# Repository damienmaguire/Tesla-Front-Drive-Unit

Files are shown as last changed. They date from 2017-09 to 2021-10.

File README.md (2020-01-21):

# Tesla-Front-Drive-Unit
Open Source Logic board to control the Tesla Model S Front Drive Unit
This board replaces the Tesla OEM control board in the high efficency front drive unit
and enables full control of the inverter and motor using simple analog / digital and CAN communication. Design files in DesignSpark 8 format.

Software may be downladed here:
https://github.com/jsphuebner/stm32-sine/releases

Fully built and tested boards and bare PCBs available here : http://www.evbmw.com/index.php/evbmw-webshop

Support forum : https://openinverter.org/forum/

23/09/17 : Released V1 schematic for the logic board. Untested. Also released pinout for the logic to igbt board interface header and Autocad dxf of the board outline with critical component locations.

02/10/17 : Released V1 design files. Untested. Unproven. Educational use only.

06/11/17 : V1 board bench tested and working well. No in car testing as yet.

29/12/17 : Uploaded V2 design files for small drive unit logic board. Compatible with both front and rear small Tesla drive units.

Just one change :

ULN2003 replaced by NCV8401ADT for driving precharge relay and main contactor following in car testing of the large drive unit.

Happy new year :)

14/08/18 : Following some excellent testing and investigation by a european customer, V3 design files are released. Small changes to component values in the current sensor opamp circuit as well as addition of two filter capacitors in the same. Now running well in vehicle. Also uploaded working parameter file.

18/10/18 : Two customers reported failures of their inverter when using the V2 board. One customer reported they had fixed the issue but then refused to share the details. I have worked with the second customer in Romania on the problems. Here are some details :

Root cause of the drive unit inverter failures discovered and fixed.
NOT caused by overcurrent through the igbts but rather the combination of using 8.8kHz switching frequency through a very low inductance stator and the sudden release of the main contactor on an overcurrent detection. The small drive unit inverter works perfectly at 17.6khz switching frequency and setting tripmode to prechon ensures the pre charge resistor can provide a path back to the battery during release of the main contactor. This was tested to the Nth degree on my recent trip to Romania

Working on a fix for a hardware bug that is limiting power. The tesla current sensors span +/- 1250A over a range of 0-5v with 2.5v representing 0A. Seems Tesla use the EXACT SAME hardware overcurrent detection circuit on their logic board as designed by Johannes. They set trip points at .1V and 4.9V giving a total span of 1200A. (1A=2mV). The component choice in the opamp circuit on the open source board causes a hardware overcurrent event at +850A regardless of settings above this value thus limiting power. It was this trip coupled with the above issues relating to main contactor control and switching frequency that lead to inverter deaths.

Identified the hall effect current sensor used in the small drive units as the MLX91209. So at least now if I wreck one they only cost 3 Euros to replace. A V4 design will be released shortly along with details on how to modify the V2 and V3 boards to avoid this problem. 

28/10/18 : V4 Design files released. Major changes : 

Updated current sensor opamp component values to allow the full +/-1200A swing.

Deleted the encoder polarity jumper as no longer needed.

Added option to fit ESP WiFi module on board (untested)

Added jumper to disable RS232 Transciever (required if using on board wifi)

Latest sourcecode and binaries will available from https://github.com/jsphuebner/stm32-sine

V2 and V3 boards can still be used by changing the following component values : R44,R49 = 62k, R48 = 3k16.

On the web interface set the following two parameters :

PWMFRQ=17.6kHz

Tripmode = Prechon

Working and tested full parameter files will be released shortly.

29/10/18 : V2 Design files and BOM updated for modifications and also incorrect values for temp sensor load resistors in BOM.

Test run with modification : https://www.youtube.com/watch?v=mhGwcPWCbsA

21/01/20 : V6 design files now released. Both fully built and partial built boards available from the EVBMW webshop : https://www.evbmw.com/index.php/evbmw-webshop
Don't want to buy from me and support ongoing development? That's ok as this release also includes the BOM, CPL and Gerber files needed to build your own at JLCPCB : https://jlcpcb.com

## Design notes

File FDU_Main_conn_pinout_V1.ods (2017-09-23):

Tesla Small Drive Unit Main Connector Pinout
Pin Number | Function | Signal Description
1 | CAN LOW | Can bus low signal
2 | CAN HIGH | Can bus high signal
3 | MAIN CONTACTOR CONTROL | Open collector control for main HVDC contactor
4 | ACCELERATOR +5V | +5v dc supply for accelerator / throttle
5 | FORWARD DIRECTION SIGNAL | When pulled to +12v motor will run forward
6 | ACCELERATOR GROUND | Ground connection for accelerator / throttle
7 | BRAKE TRANSDUCER GROUND | Ground connection for brake pedal position sensor
8 | ACCELERATOR SIGNAL | Input for accelerator / throttle signal. 0-3.3v span.
9 | START SIGNAL | Starts the inverter when connected briefly to +12v. Typically connected to “Start” position on car ignition switch
10 | BRAKE TRANSDUCER SIGNAL | Signal from brake pedal position sensor. 0-3.3v span. Controls regen relative to brake pedal position
11 | PRECHARGE RELAY CONTROL | Open collector control for main HVDC precharge relay
12 | REVERSE DIRECTION SIGNAL | When pulled to +12v motor will run in reverse
13 | +12V SUPPLY IGN ON | Main +12v dc supply to inverter
14 | RS232 Rx | Serial receive line for RS232 communication
15 | BRAKE ON DIGITAL SIGNAL | +12v signal to inverter that brake pedal is pressed
16 | RS232 Tx | Serial transmit line for RS232 communication
17 | CRUISE CONTROL SIGNAL | Toggles cruise control on and off with +12v momentary signal
18 | BRAKE TRANSDUCER +5V | +5v dc supply for brake pedal position transducer
19 | GROUND | Main system ground to chassis of vehicle
20 | TACHOMETER DRIVE SIGNAL | Open collector variable frequency drive for standard tachometer

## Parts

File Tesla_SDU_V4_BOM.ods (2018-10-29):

Tesla Small Drive Unit Logic Board V4
Ref Name | Qty | Component | Value | Manufacturer | MPN | Farnell Part Number | Mouser Part number | Description
CONN7,9,8,SWPROG | 4 | 2SIL |  | AMPHENOL FCI | 77311-401-36LF | 1097954 |  | Board-To-Board Connector, 2.54 mm, 36 Contacts, Header, BergStik 77311 Series, Through Hole, 1 Rows
CONN10 | 1 | 75867-101LF |  | FCI | 75867-101LF | 6737635 |  | 10w R/A T/H boxed header Quickie Amphenol FCI Quickie Series, 2.54mm Pitch 10 Way 2 Row Shrouded Right Angle PCB Header, Through Hole
IC11 | 1 | 74HCT4052D |  | NXP | 74HCT4052D | 4836730 |  | 74HCT4052D, Multiplexer/Demultiplexer Dual 4:1, 5 V, 16-Pin, SOIC, 2
CONN2 | 1 | 75757-5101 |  | Molex | 75757-5101 |  | 538-75757-5101 | Headers & Wire Housings MX150 2X10 VERT HEAD HEADER ASSY 2.5 TIN
L1 | 1 | 7447709470 |  | Wurth Elektronik | 7447709470 | 1635946 |  | SMD-Shielded Power Inductors WE-PD
IC10 | 1 | ADM3101EARQZ |  | Analog Devices | ADM3101EARQZ | 7097966 |  | ADM3101EARQZ, Line Transceiver, EIA-232-E, RS-232, V.28, 3.3 V, 16-Pin QSOP
C41,23,24,106,44,42,43,45,36,4,8,10,11,16,65 | 15 | C-USC0805 | 0.1uF | MURATA | GRM219R71C104KA01D | 2611934 |  | Murata 0805 GRM 100nF Ceramic Multilayer Capacitor, 16 V dc X7R Dielectric ±10% SMD
C18,19,20,33,34 | 5 | C-USC0805 | 1nF | MULTICOMP | MCSH21B102K160CT | 1856432 |  | SMD Multilayer Ceramic Capacitor, 0805 [2012 Metric], 1000 pF, 16 V, ± 10%, X7R, MCSH Series
C21,22,25,26,28,29,30,31,32,57,58,59,60,61,62,6,7,14,15,37 | 20 | C-USC0805 | 1uF | KEMET | C0805C105K4RACTU | 9227792 |  | Kemet 0805 1μF Ceramic Multilayer Capacitor, 16V dc X7R Dielectric ±10% SMD
C46,47,48,49,50 | 5 | C-USC0805 | 10nF | Wurth Elektronik | 885012207039 | 2534055 |  | SMD Multilayer Ceramic Capacitor, 0805 [2012 Metric], 0.01 µF, 16 V, ± 10%, X7R,
C1,2 | 2 | C-USC0805 | 27pF | MULTICOMP | MC0805N270J500CT | 1759196 |  | SMD Multilayer Ceramic Capacitor, 0805 [2012 Metric], 27 pF, 50 V, ± 5%, C0G / NP0, MC Series
C105 | 1 | C-USC0805 | 47nF | YAGEO (PHYCOMP) | CC0805KRX7R9BB473 | 718683 |  | SMD Multilayer Ceramic Capacitor, 0805 [2012 Metric], 0.047 µF, 50 V, ± 10%, X7R, CC Series
C3 | 1 | Cap_el | 100uF | MULTICOMP | MCMR6V3107M6.3X7 | 9452567 |  | Electrolytic Capacitor, 100 µF, 6.3 V, MCMHR Series, ± 20%, Radial Leaded, 6.3 mm
IC5 | 1 | CD74HC30M |  | Texas Instruments | CD74HC30M | 526824 |  | CD74HC30M, Logic Gate 8 Input NAND, HC, 5.2mA 2 to 6V 14-Pin SOIC
X2 | 1 | CRYSTALTC26HM | 32.768kHz | RALTRON | R26-32.768- 12.5 | 1652573 |  | Crystal, 32.768 kHz, Cylinder Radial, 6.2mm x 2mm Dia, 12.5 pF, 20 ppm, R26 Series
C12,13 | 2 | C_0805 | 10pF | Wurth Elektronik | 885012007010 | 2533859 |  | SMD Multilayer Ceramic Capacitor, 0805 [2012 Metric], 10 pF, 16 V, ± 5%, C0G / NP0
C5,9,17 | 3 | C_0805 | 10uF | MURATA | GRM21BR61E106KA73L | 1735530 |  | SMD Multilayer Ceramic Capacitor, 0805 [2012 Metric], 10 µF, 25 V, ± 10%, X5R, GRM Series
C38 | 1 | EEEFK1A221XP | 220uF | Panasonic | EEEFK1A221XP | 7083342 |  | Ecap 220uF 10V D8 Case FK SMD Panasonic 220F 10 V dc Aluminium Electrolytic Capacitor, FK SMD Series 2000h 6.3 Dia. x 7.7mm
C35 | 1 | EEVEB2C680SM | 680uF | Panasonic | EEVEB2C680SM | 2326340 | 667-EEV-EB2C680SM | PANASONIC ELECTRONIC COMPONENTS - EEVEB2C680SM - CAP, ALU ELEC, 68UF, 160V, SMD
C27,39 | 2 | C-USC0805 | 50pF | YAGEO (PHYCOMP) | CC0805JRNPO9BN470 | 1362560 |  | SMD Multilayer Ceramic Capacitor, 0805 [2012 Metric], 47 pF, 50 V, ± 5%, C0G / NP0, CC Series
CONN1 | 1 | FDU_IGBT_CONN |  | 3M | 929975-01-36 | 828-2058 |  | 3M 929 Series 929975 Series Number 2.54mm Pitch 72 Way 2 Row Straight PCB Header
LD1 | 1 | LD1117SOT223 | LD1117-3.3 | STMICROELECTRONICS | LD1117S33CTR | 1467779 |  | Fixed LDO Voltage Regulator, 4.75V to 15V, 1.1V Dropout, 3.3Vout, 950mAout, SOT-223-4
LED1,2 | 2 | LED0805 |  | MULTICOMP | MCL-S270GC | 1581242 |  | LED, Green, SMD, 1.25mm x 1.4mm, 20 mA, 2.1 V, 570 nm
X1 | 1 | LFXTAL011301 | 8.00MHz | IQD | LFXTAL011301 | 4789656 |  | Crystal SMD 8.000MHz HC49S-SMD Crystal 8MHz, 30ppm, 2-Pin HC-49-4H-SMX
IC8 | 1 | LM2596S-5.0_NOPB |  | Texas Instruments | LM2596S-5.0/NOPB | 5333692 |  | SIMPLE SWITCHER 4.5V to 40V, 3A Low Component Count Step-Down Regulator
IC4 | 1 | LM2901DT |  | STMicroelectronics | LM2901DT | 7140745 |  | LM2901DT, Quad Comparator Open Collector 1.3s 12 V, 15 V, 18 V, 24 V, 28 V, 3 V, 5 V, 9 V 14-Pin SO
L2 | 1 | L_PM0603 | 10uH | TDK | MLZ1608M100WT | 2215635 |  | Surface Mount High Frequency Inductor, MLZ Series, 10 µH, 250 mA, 0603 [1608 Metric], Multilayer
D1,D2 | 2 | MBRS540T3G |  | ON Semiconductor | MBRS540T3G | 1250012 |  | Diode Schottky 40V 5A SMC ON Semiconductor MBRS540T3G Schottky Diode, 5A, 40V, 2-Pin SMC
IC12 | 1 | MC74HCT573ADWR2G |  | ON Semiconductor | MC74HCT573ADWR2G | 2814898 | 863-MC74HCT573ADWR2G | TRANSPARENT LATCH, OCTAL, SOIC-20
IC7 | 1 | MCP602-I_SN |  | Microchip | MCP602-I/SN | 3792588 |  | Operational Amplifier, Dual, 2 Amplifier, 2.8 MHz, 2.3 V/µs, 2.7V to 5.5V
Q1 | 1 | MMBT3904 |  | Fairchild Semiconductor | MMBT3904 | 7390303 |  | Transistor GP BJT NPN 40V 0.2A SOT23 Fairchild MMBT3904 NPN Bipolar Transistor, 0.2 A, 40 V, 3-Pin SOT-23
R8,6,38,39,40,41,43,35 | 8 | R-US_R0805 | 1k | MULTICOMP | MC01W080551K | 9333711 |  | SMD Chip Resistor, Thick Film, 1 kohm, 150 V, 0805 [2012 Metric], 100 mW, ± 5%, MC Series
R24,26,28,32,33 | 5 | R-US_R0805 | 1K5 | Panasonic | ERJ6RBD1501V | 2380317 |  | SMD Chip Resistor, Thick Film, 1.5 kohm, 150 V, 0805 [2012 Metric], 100 mW, ± 0.5%, ERJ6E Series
R3,7,17 | 3 | R-US_R0805 | 3K3 | Panasonic | ERJ6RBD3301V | 2380370 |  | SMD Chip Resistor, Thick Film, 3.3 kohm, 150 V, 0805 [2012 Metric], 100 mW, ± 0.5%, ERJ6E Series
R48 | 1 | R-US_R0805 | 3K16 | Panasonic | ERJ6ENF3161V | 2303602 |  | SMD Chip Resistor, 3.16 kohm, ERJ6E Series, 150 V, Thick Film, 0805 [2012 Metric], 125 mW
R47,23,25,27,31,34,11 | 7 | R-US_R0805 | 4K7 | Panasonic | ERJ6RBD4701V | 2380397 |  | SMD Chip Resistor, Thick Film, 4.7 kohm, 150 V, 0805 [2012 Metric], 100 mW, ± 0.5%, ERJ6E Series
R2,4,9,10,12,14,15,46,51,1,18,19,20,21,29,30,36,37,13,22 | 20 | R-US_R0805 | 10k | BOURNS | CRT0805-FZ-1002ELF | 2008317 |  | SMD Chip Resistor, Thin Film, 10 kohm, 100 V, 0805 [2012 Metric], 100 mW, ± 1%, CRT Series
R65 | 1 | R-US_R0805 | 470K | VISHAY | CRCW0805470KFKEA | 1653006 |  | SMD Chip Resistor, 470 kohm, CRCW Series, 150 V, Thick Film, 0805
R16 | 1 | R-US_R0805 | 47K | Panasonic | ERJ6RBD4702V | 2380398 |  | SMD Chip Resistor, Thick Film, 47 kohm, 150 V, 0805 [2012 Metric], 100 mW, ± 0.5%, ERJ6E Series
R55,62,63,64,66 | 5 | R-US_R0805 | 150K | YAGEO (PHYCOMP) | RC0805FR-07150KL | 9237895 |  | SMD Chip Resistor, 150 kohm, RC Series, 150 V, Thick Film, 0805
R69,70 | 2 | R-US_R0805 | 60R4 | TE CONNECTIVITY | RN73C2A60R4BTDF | 2688288RL |  | SMD Chip Resistor, Precision, 60.4 ohm, 100 V, 0805 [2012 Metric], 100 mW, ± 0.1%
R45,50 | 2 | R-US_R0805 | 100K | MULTICOMP | MC01W08055100K | 9333738 |  | SMD Chip Resistor, 100 kohm, 150 V, 0805 [2012 Metric], 100 mW, ± 5%, MC Series
R44,49 | 2 | R-US_R0805 | 62K | VISHAY | CRCW080562K0FKEA | 2139013 |  | SMD Chip Resistor, 62 kohm, CRCW Series, 150 V, Thick Film, 0805 [2012 Metric], 125 mW
R42 | 1 | R-US_R0805 | 100R | MULTICOMP | MC01W08055100R | 9333703 |  | SMD Chip Resistor, Thick Film, 100 ohm, 100 V, 0805 [2012 Metric], 100 mW, ± 5%, MC Series
R5 | 1 | R-US_R0805 | 470R | Panasonic | ERJ6RBD4700V | 2380396 |  | SMD Chip Resistor, Thick Film, 470 ohm, 150 V, 0805 [2012 Metric], 100 mW, ± 0.5%, ERJ6E Series
R56,57,58,59,60 | 5 | R-US_R0805 | 560R | VISHAY | CRCW0805560RFKEA | 1469945 |  | SMD Chip Resistor, Thick Film, 560 ohm, 150 V, 0805 [2012 Metric], 125 mW, ± 1%
CONN3,4 | 2 | S02BA-AIT2-1AK |  | JST Automotive | S02BA-AIT2-1AK |  | 306-S02BA-AIT2-1AK | Automotive Connectors 2P BLK Side Entry Brs tin plated pin
CONN5 | 1 | S06B-AIT2-1AK |  | JST Automotive | S06B-AIT2-1AK |  | 306-S06B-AIT2-1AK | Automotive Connectors 6CIR BLK SNGL ROW SIDE ENTRY
IC9 | 1 | SN65HVD234 | SN65HVD234 | TEXAS INSTRUMENTS | SN65HVD234D | 1212363 |  | CAN Bus, Transceiver, CAN, 1, 1, 3 V, 3.6 V, SOIC
IC1 | 1 | STM32F103 | STM32F103RBT6 | STMICROELECTRONICS | STM32F103RBT6 | 1447640 |  | ARM Microcontroller, Motor Control, ARM Cortex-M3, 32bit, 72 MHz, 128 KB, 20 KB, 64 Pins
CONN6 | 1 | T821120A1S100CEU |  | AMPHENOL | T821120A1S100CEU | 8323499 |  | HEADER, VERTICAL, 2.54MM, 20WAY
IC13,IC14 | 2 | NCV8401ADTRKG |  | ON Semiconductor | NCV8401ADTRKG | 8079877 |  | Power Load Distribution Switch IC, Low Side, 1 Output, ± 14 V in, 16 A, 0.034 ohm

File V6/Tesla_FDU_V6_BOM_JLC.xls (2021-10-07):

Comment | Designator | Footprint | LCSC Part #
74HCT4052D | IC6 | SOIC-16_3.9x9.9x1.27P | C87281
BTS133TC | IC9,IC11 | TO-263-2 | C152447
0.1uF | C4,C13,C20,C39,C28,C30,C1,C2,C6,C13,C35,C52 | 0805_C | C49678
1nF | C18,C22,C29,C8,C5 | 0805_C | C46653
1uF | C27,C25,C32,C19,C17,C21,C40,C42,C45,C43,C46,C41,C44,C14,C11,C38,C36,C31,C37,C51 | 0805_C | C28323
10nF | C16,C9,C10,C12,C15 | 0805_C | C1710
22PF | C23,C24 | 0805_C | C1804
50pF | C3,C7 | 0805_C | C1716
CD74HC30M | IC5 | SOIC-14_3.9x8.7x1.27P | C5631
10pF | C26,C33 | C_0805 | C1785
10uF | C34,C48 | 0805_C | C15850
LD1117-3.3 | LD1 | SOT-223 | C347229
RED LEDS | LED1,LED2 | CHIPLED_0805 | C84256
5V REG | IC12 | TO-263-5 | C10002
LM2901DT | IC4 | SOIC-14_3.9x8.7x1.27P | C142961
10uH | L1 | 0603 | C1035
MC74HCT573ADWR2G | IC7 | SOIC-20_7.5x12.8x1.27P | C6000
MCP602-I_SN | IC3 | SOIC-8_3.9x4.9x1.27P | C29605
MMBT3904 | Q1 | SOT-23-3 | C20526
1KΩ | R23,R28,R39,R40,R34,R32,R38 | 0805_R | C17513
1.5KΩ | R43,R47,R53,R49,R55 | 0805_R | C4310
3.3KΩ | R31,R12,R10 | 0805_R | C26010
3.16KΩ | R7 | 0805_R | C52603
4.7KΩ | R36,R42,R46,R52,R48,R54,R8 | 0805_R | C17673
10KΩ | R5,R6,R22,R25,R44,R50,R45,R51,R20,R16,R15,R3,R1,R61,R60,R59,R58,R57,R56,R35 | 0805_R | C17414
47kΩ | R62 | 0805_R | C17713
62KΩ | R9,R11 | 0805_R | C17783
100KΩ | R2,R4 | 0805_R | C17407
100Ω | R27 | 0805_R | C17408
120Ω | R37 | 0805_R | C17437
150kΩ | R30,R33,R24,R21,R26 | 0805_R | C17470
470Ω | R41 | 0805_R | C17710
470kΩ | R29 | 0805_R | C17709
560Ω | R18,R13,R14,R17,R19 | 0805_R | C28636
SN65HVD234 | IC10 | SOIC-8_3.9x4.9x1.27P | C99818
SS54 | D1,D2 | SMA,DO-214AC | C22452
STM32F103RBT6 | IC8 | LQFP-64_10.0x10.0x0.5P | C8735
470UH | L2 | SMD-PIND-12.5x12.5x8_2.9x5.4 | C169382
100UF 6.3V | C50,C49,C47 | CASE-B_3528 | C16133
470uF 25V | C53 | SMD-ECAP-10x10 | C249931
8MHz | X1 | SMD-5032_2P | C115962

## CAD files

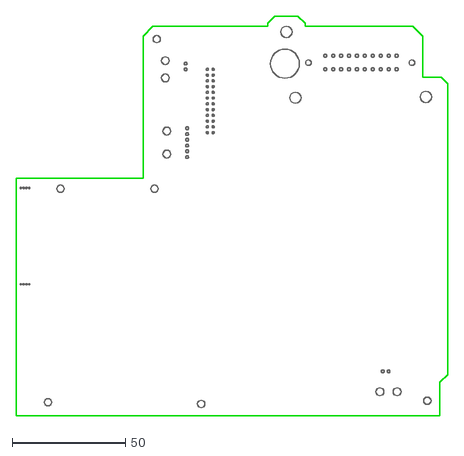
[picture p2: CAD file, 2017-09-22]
Tesla_FDU_V1.dxf
190.5 x 176.5

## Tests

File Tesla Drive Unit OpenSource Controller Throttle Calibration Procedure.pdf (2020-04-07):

## Tesla Drive Unit OpenSource Controller Throttle Calibration Procedure

Now to calibrate the throttle pedal so the inverter knows the range to expect.
Power on the inverter 12v supply (no High voltage needed at this point) and connect with WiFi.
The default WiFi settings are :
SSID : inverter
Passphrase : inverter123
Open a Web browser and enter 192.168.1.4 in the address bar and press enter.
Ensure the throttle pedal is properly connected to the inverter using pins 12 (+5V), 13 (signal), and 15 (ground).

With the throttle pedal at zero (ie no pressure on the pedal) scroll down to the “Pot”
Spot value on the webpage (make sure to refresh the webpage by pressing F5 or the “refresh” button). Make a note of this value.
Now press the throttle fully and repeat this process, again observing the ‘pot’ spot value.
Note this value. You now have the two values representing no throttle and full throttle.

Under the ‘Throttle’ category on the web interface, find the “PotMin” parameter and enter the value you recorded for zero throttle position (it is a good idea to make this value a few points less to allow for noise. So if you recorded 850 then put in 830 for “PotMin”). Don’t forget to press enter. Now find “PotMax” and do the same as above but use the full throttle value. Press enter.

Scroll to the top and click the “Save parameters to flash” button.
Turn the 12v power to the inverter off and then on after a few seconds and check the throttle value is now correct.

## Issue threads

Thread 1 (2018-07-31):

C35 Footprint is smaller than the component. Components around it touch with it.

annerajb, 2018-07-31:
Hey,

Got around to build your board (currently trying to program/flash)
Found a issue The footprint area for the C35 part is smaller than the actual part (or the part number is incorrect) There are two versions of that Capacitor one is 16.5 MM tall the other one is 18.9MM (and smaller diameter)

The bom calls for the 16.5MM tall one which makes it wider and touches / dosn't fir the pcb layout under it.

I would fix it but not sure if it's a part number mistake, foot print is incorrect or is there any other intended reason for this.

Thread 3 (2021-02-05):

C47 not connected to ground. Incorrect net.

Bedz01, 2021-02-05:
I was testing a PCB that I just put together and noticed the capacitor C47 is not connected to ground.
I looked the the schematic and it turns out that the "GND" symbol is not assigned to the GND net, but rather to N0165.
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

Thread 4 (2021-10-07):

BOM and CPL files no longer valid for JLCPCB SMT quoting

DocOnGitHub, 2021-10-07:
Recently JLCPCB has changed the headers in their BOM and CPL files to use the term "Footprint" instead of "Package". The current files produce this error on upload:

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

Closed 2021-10-07.

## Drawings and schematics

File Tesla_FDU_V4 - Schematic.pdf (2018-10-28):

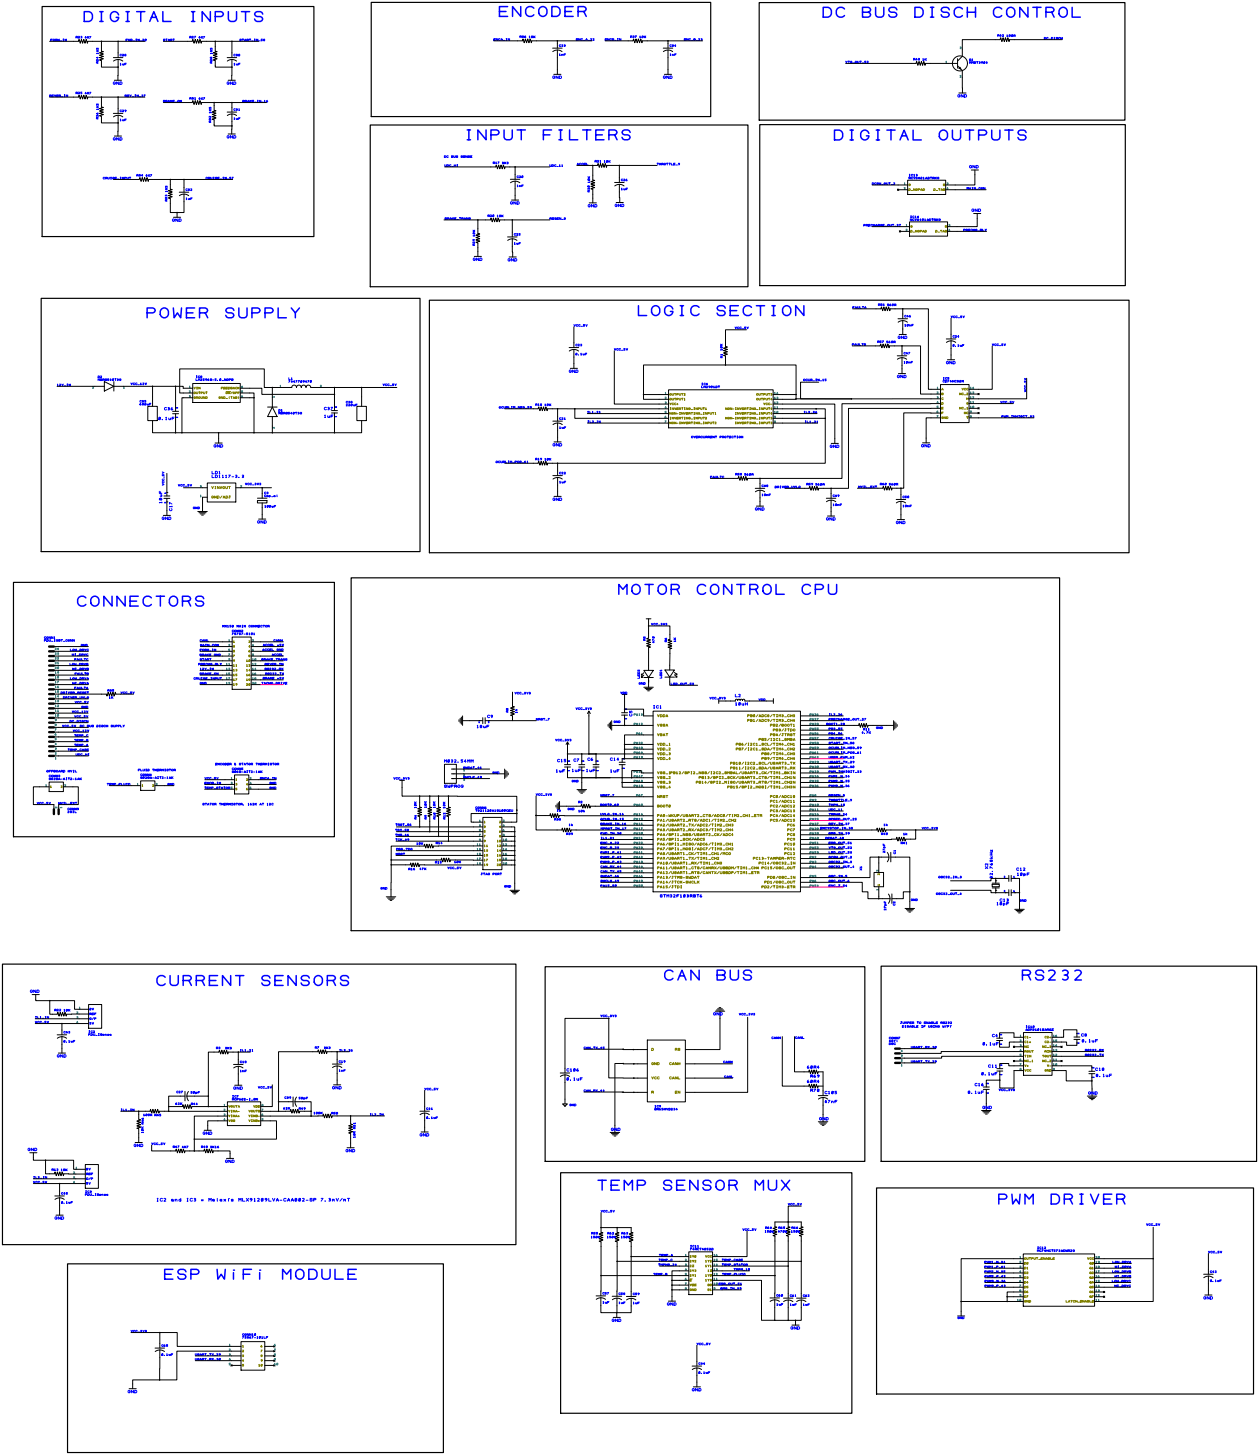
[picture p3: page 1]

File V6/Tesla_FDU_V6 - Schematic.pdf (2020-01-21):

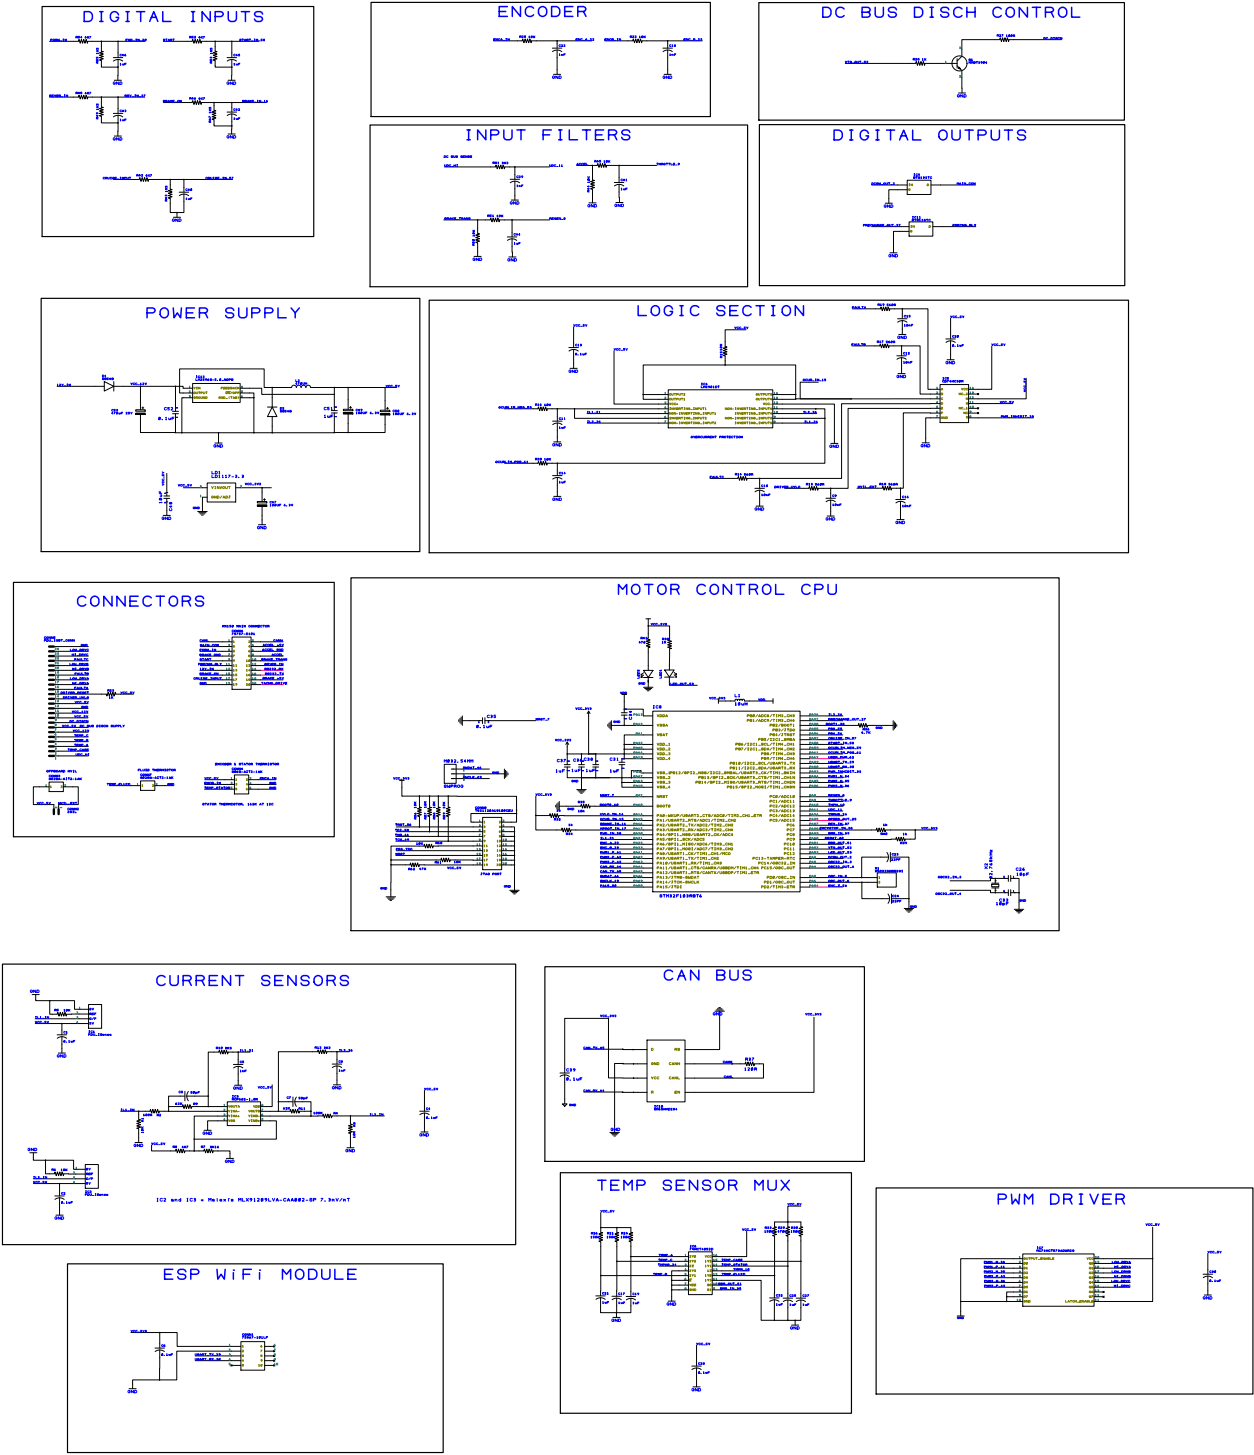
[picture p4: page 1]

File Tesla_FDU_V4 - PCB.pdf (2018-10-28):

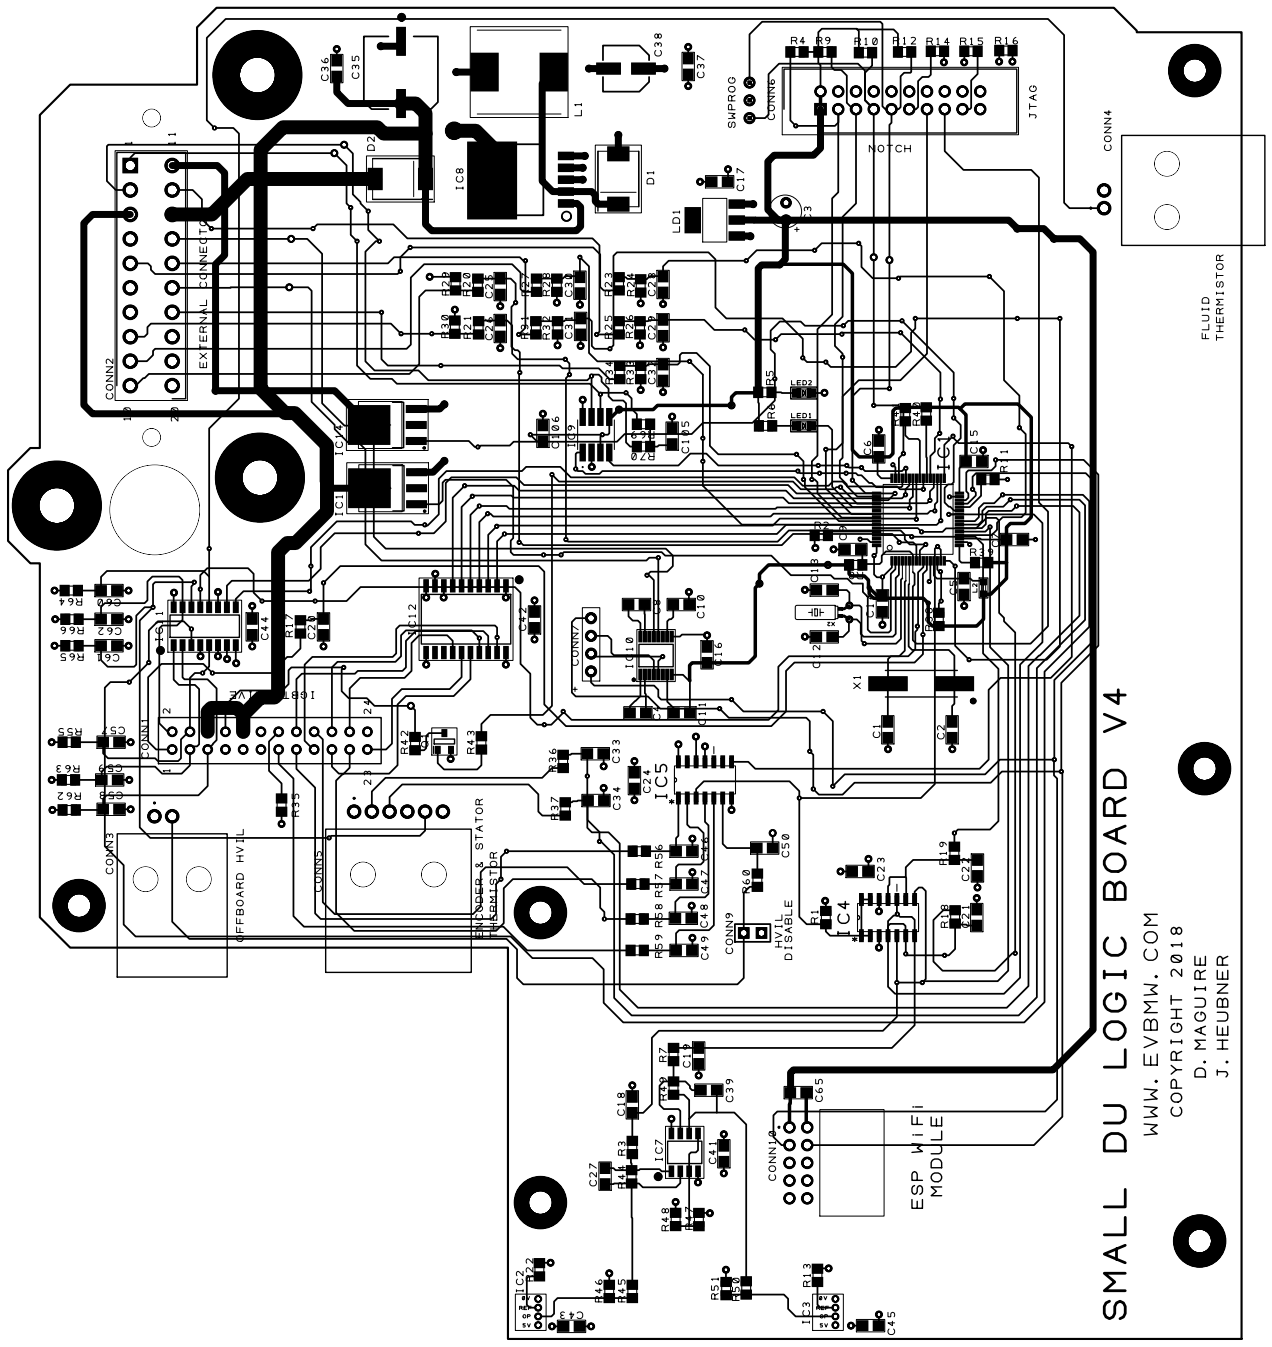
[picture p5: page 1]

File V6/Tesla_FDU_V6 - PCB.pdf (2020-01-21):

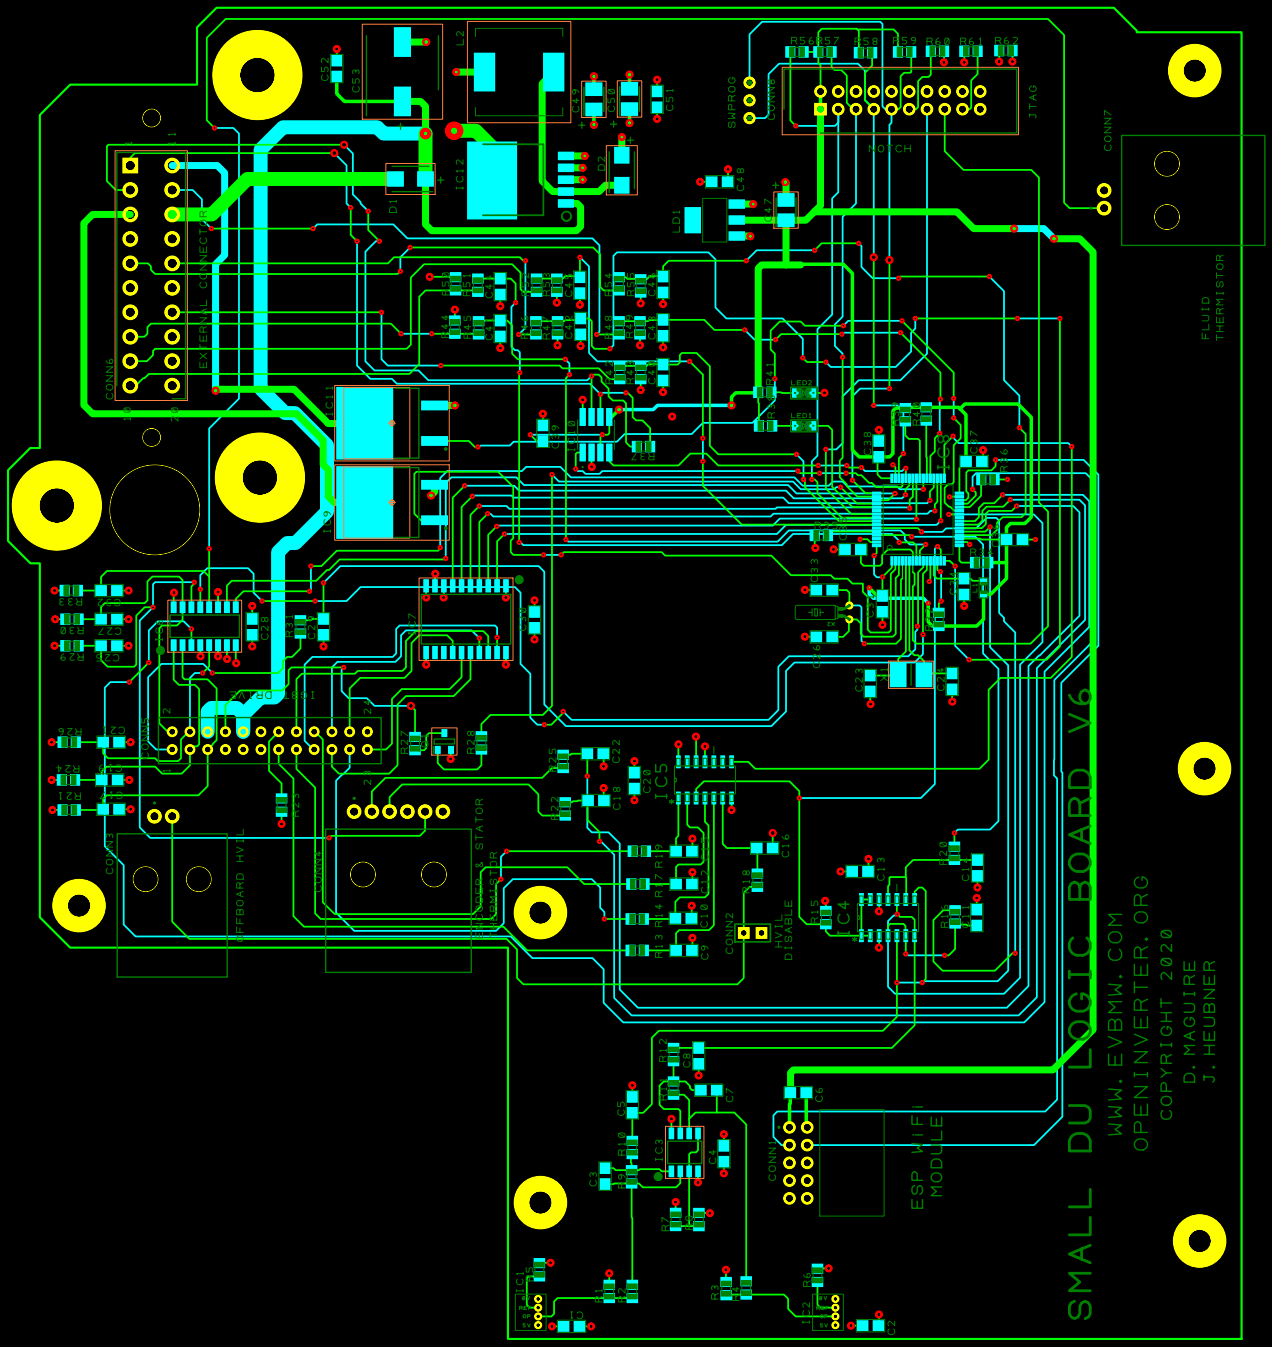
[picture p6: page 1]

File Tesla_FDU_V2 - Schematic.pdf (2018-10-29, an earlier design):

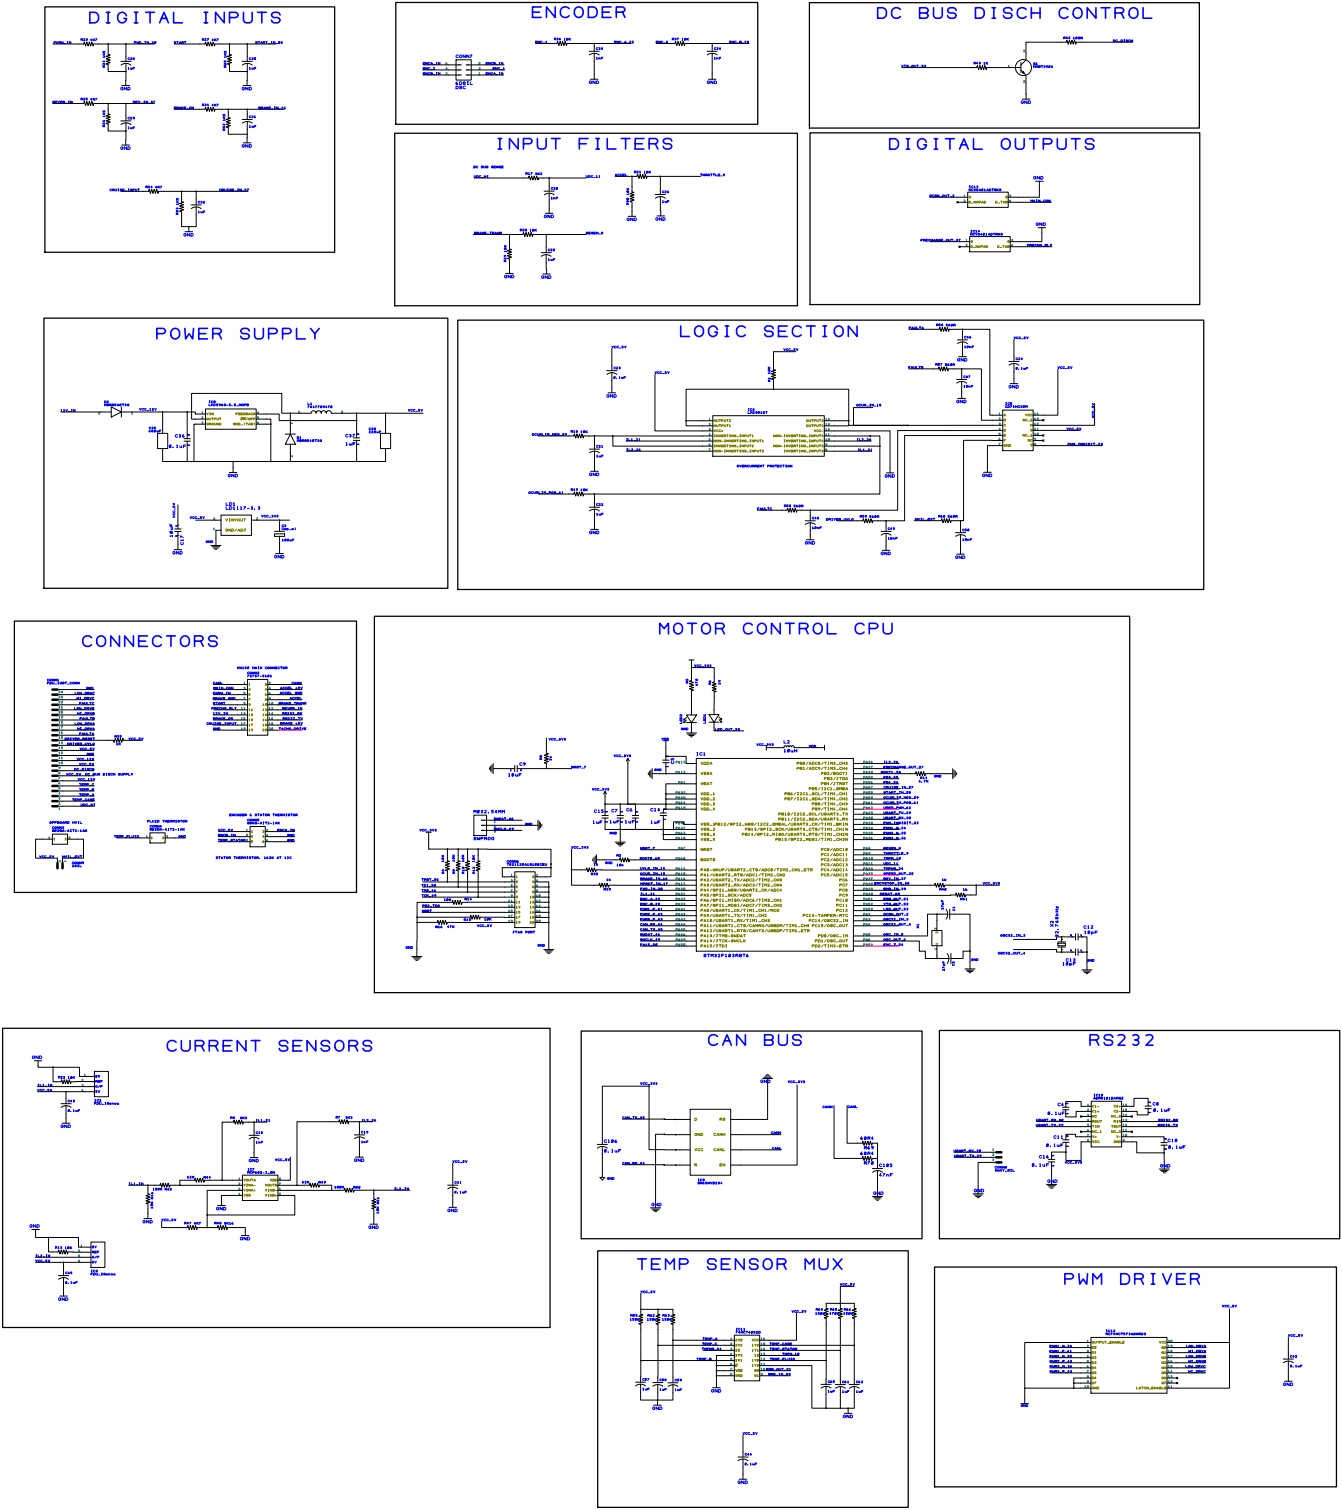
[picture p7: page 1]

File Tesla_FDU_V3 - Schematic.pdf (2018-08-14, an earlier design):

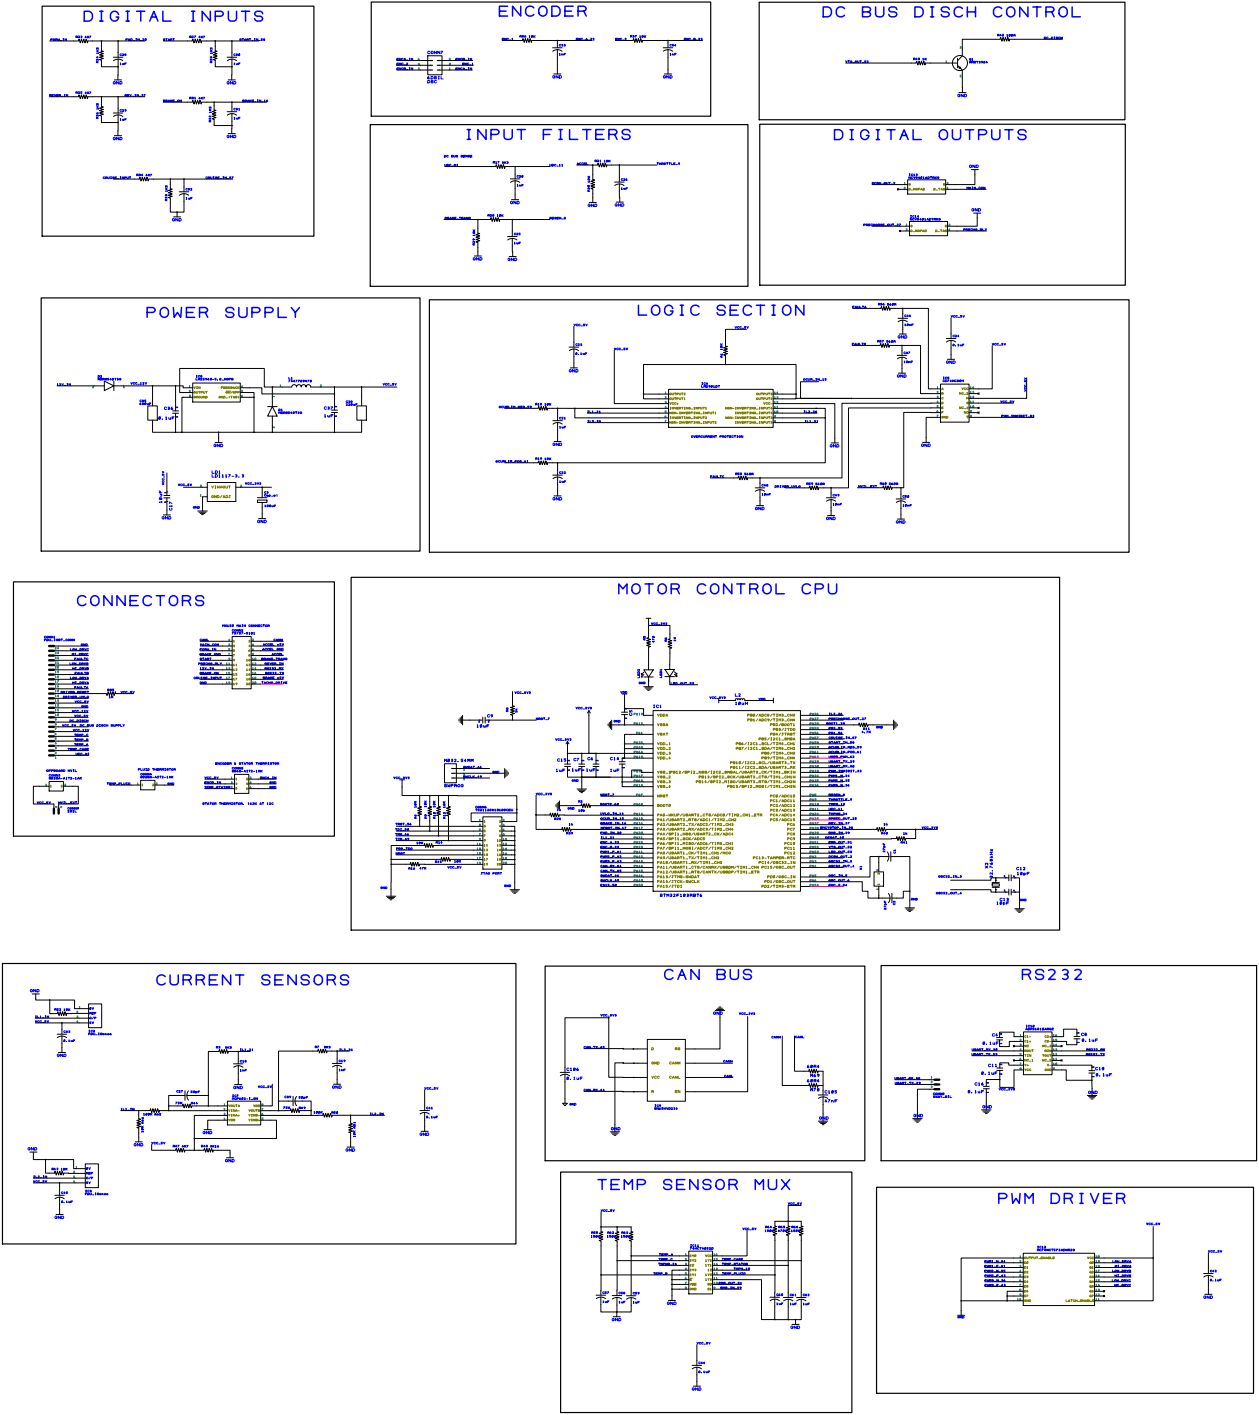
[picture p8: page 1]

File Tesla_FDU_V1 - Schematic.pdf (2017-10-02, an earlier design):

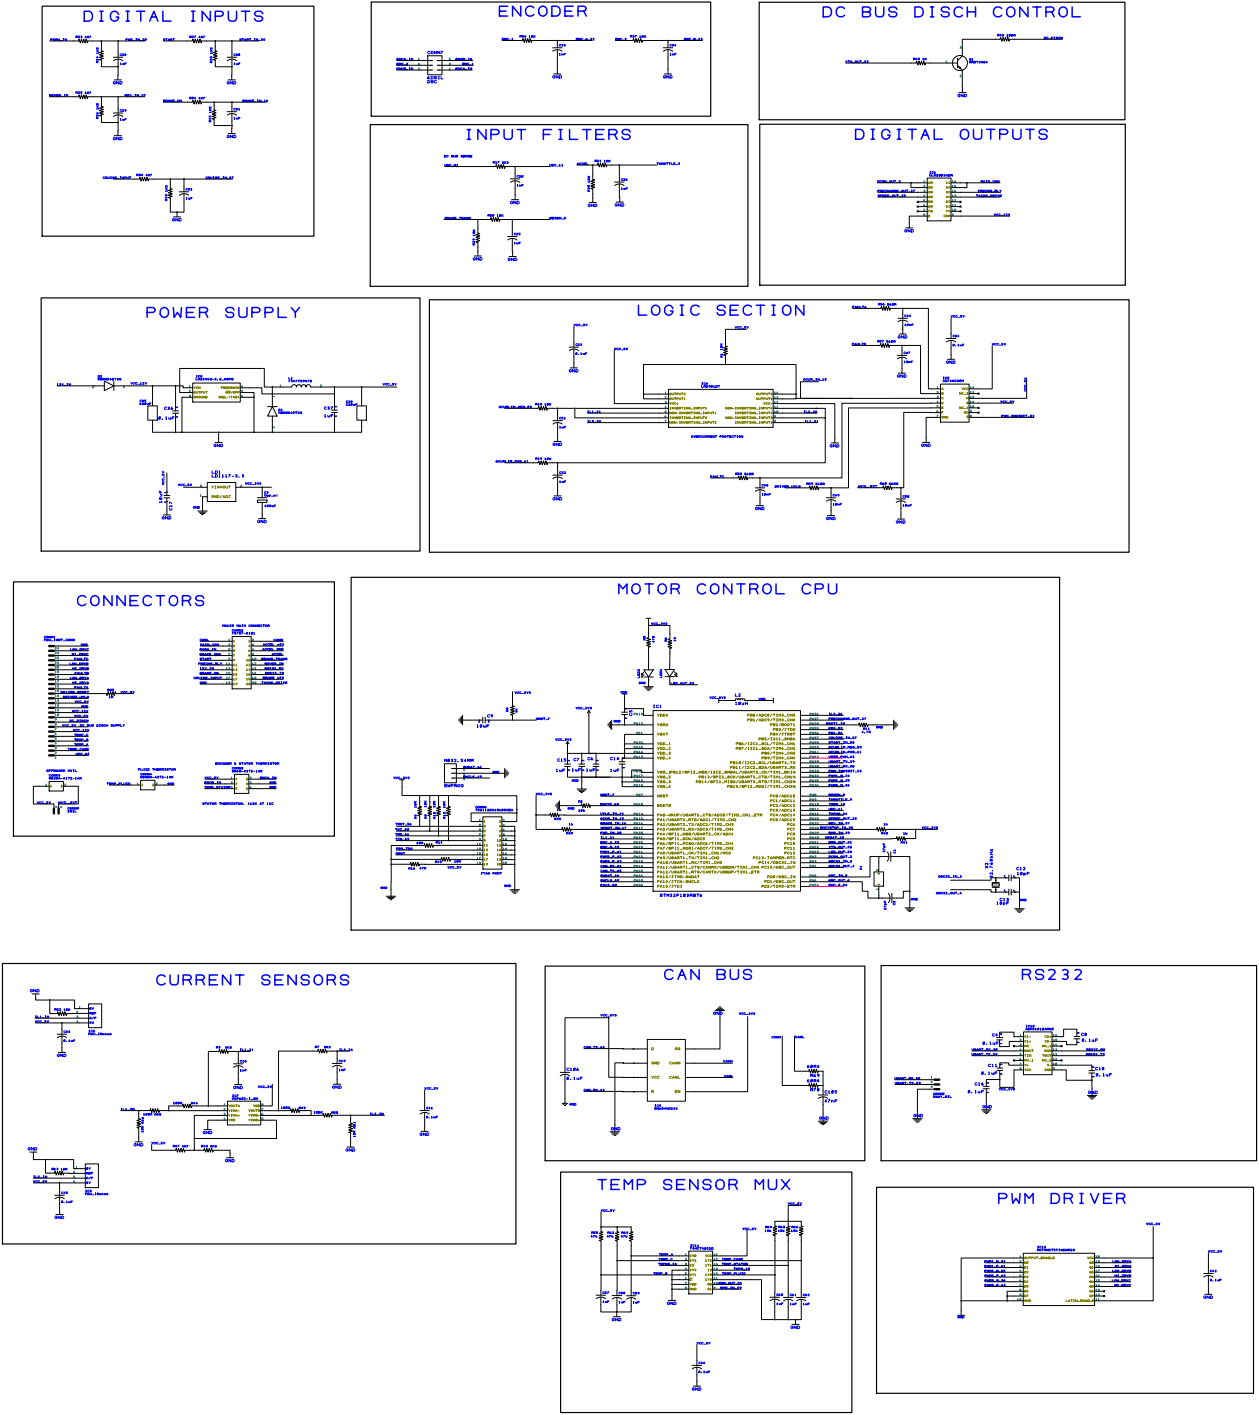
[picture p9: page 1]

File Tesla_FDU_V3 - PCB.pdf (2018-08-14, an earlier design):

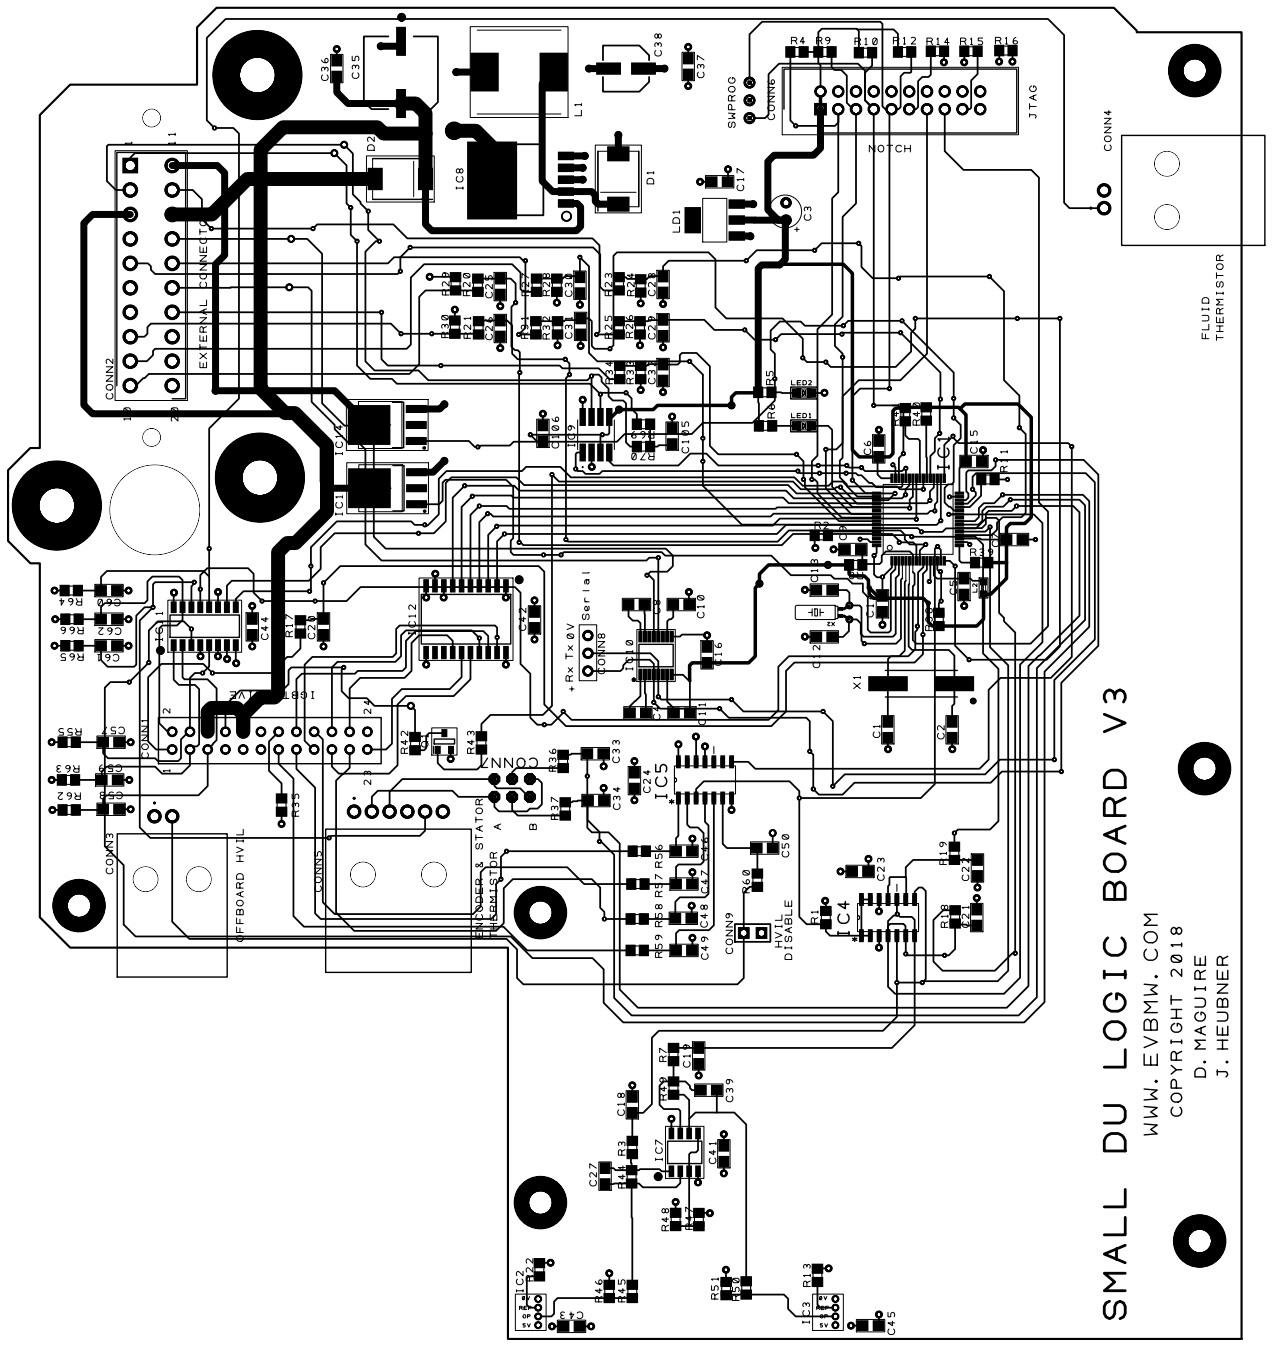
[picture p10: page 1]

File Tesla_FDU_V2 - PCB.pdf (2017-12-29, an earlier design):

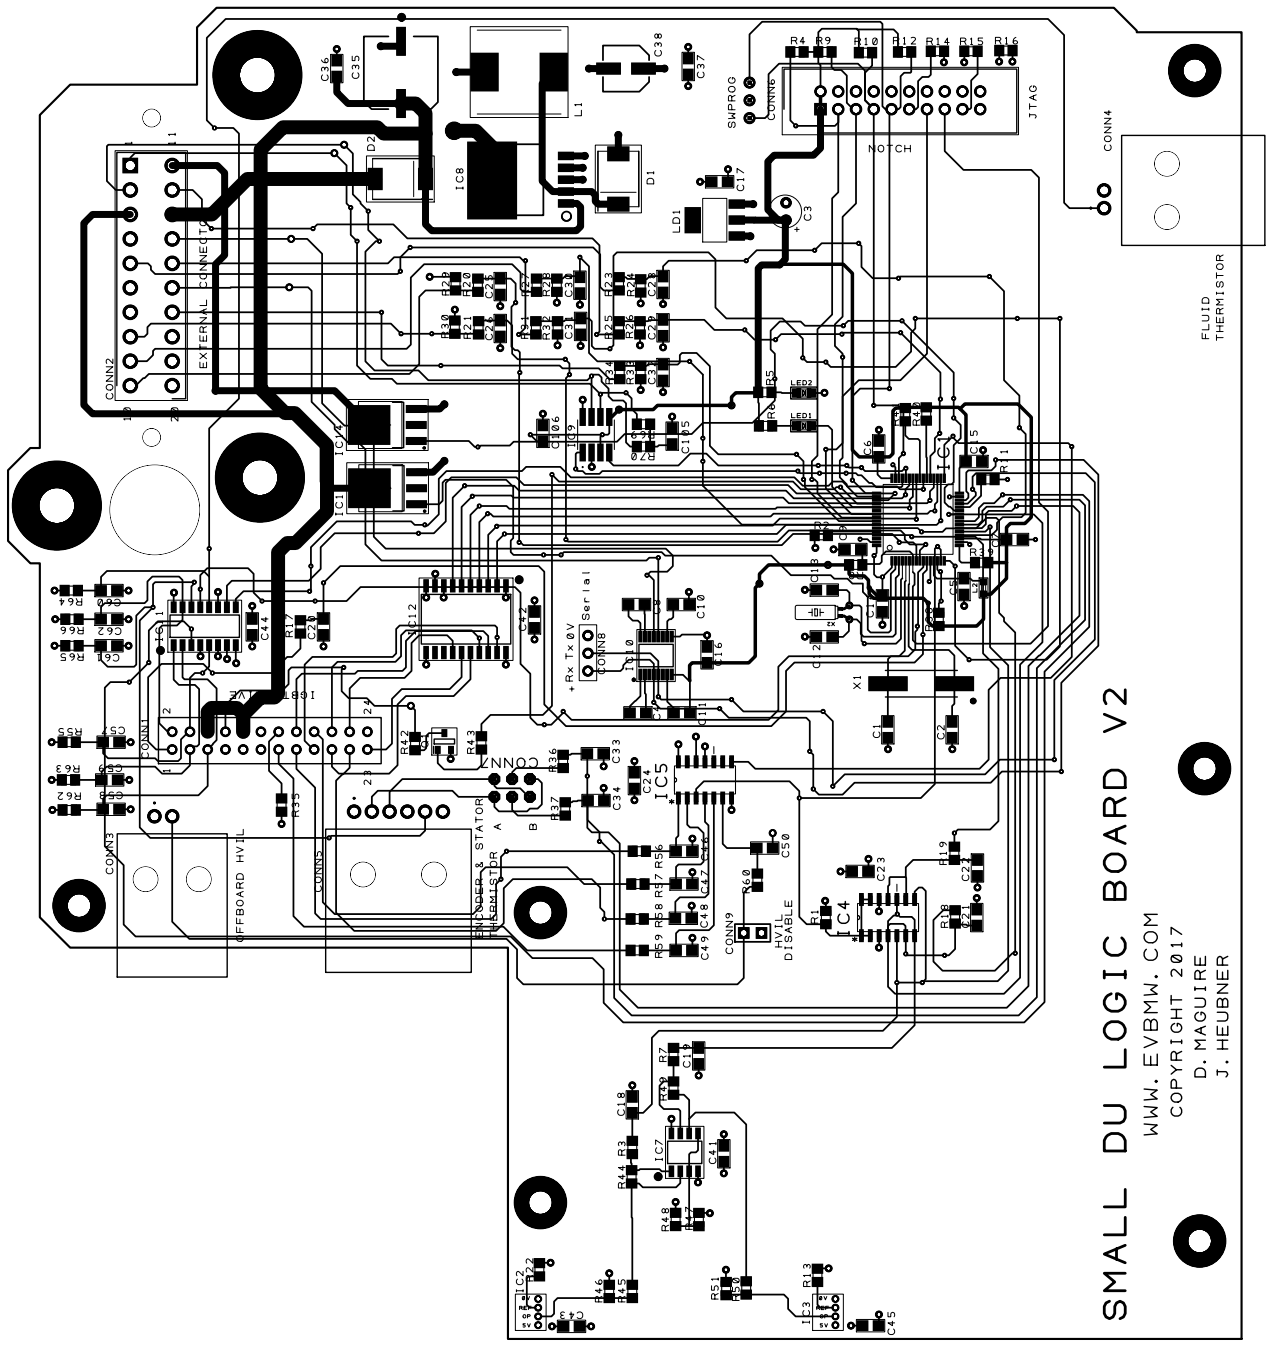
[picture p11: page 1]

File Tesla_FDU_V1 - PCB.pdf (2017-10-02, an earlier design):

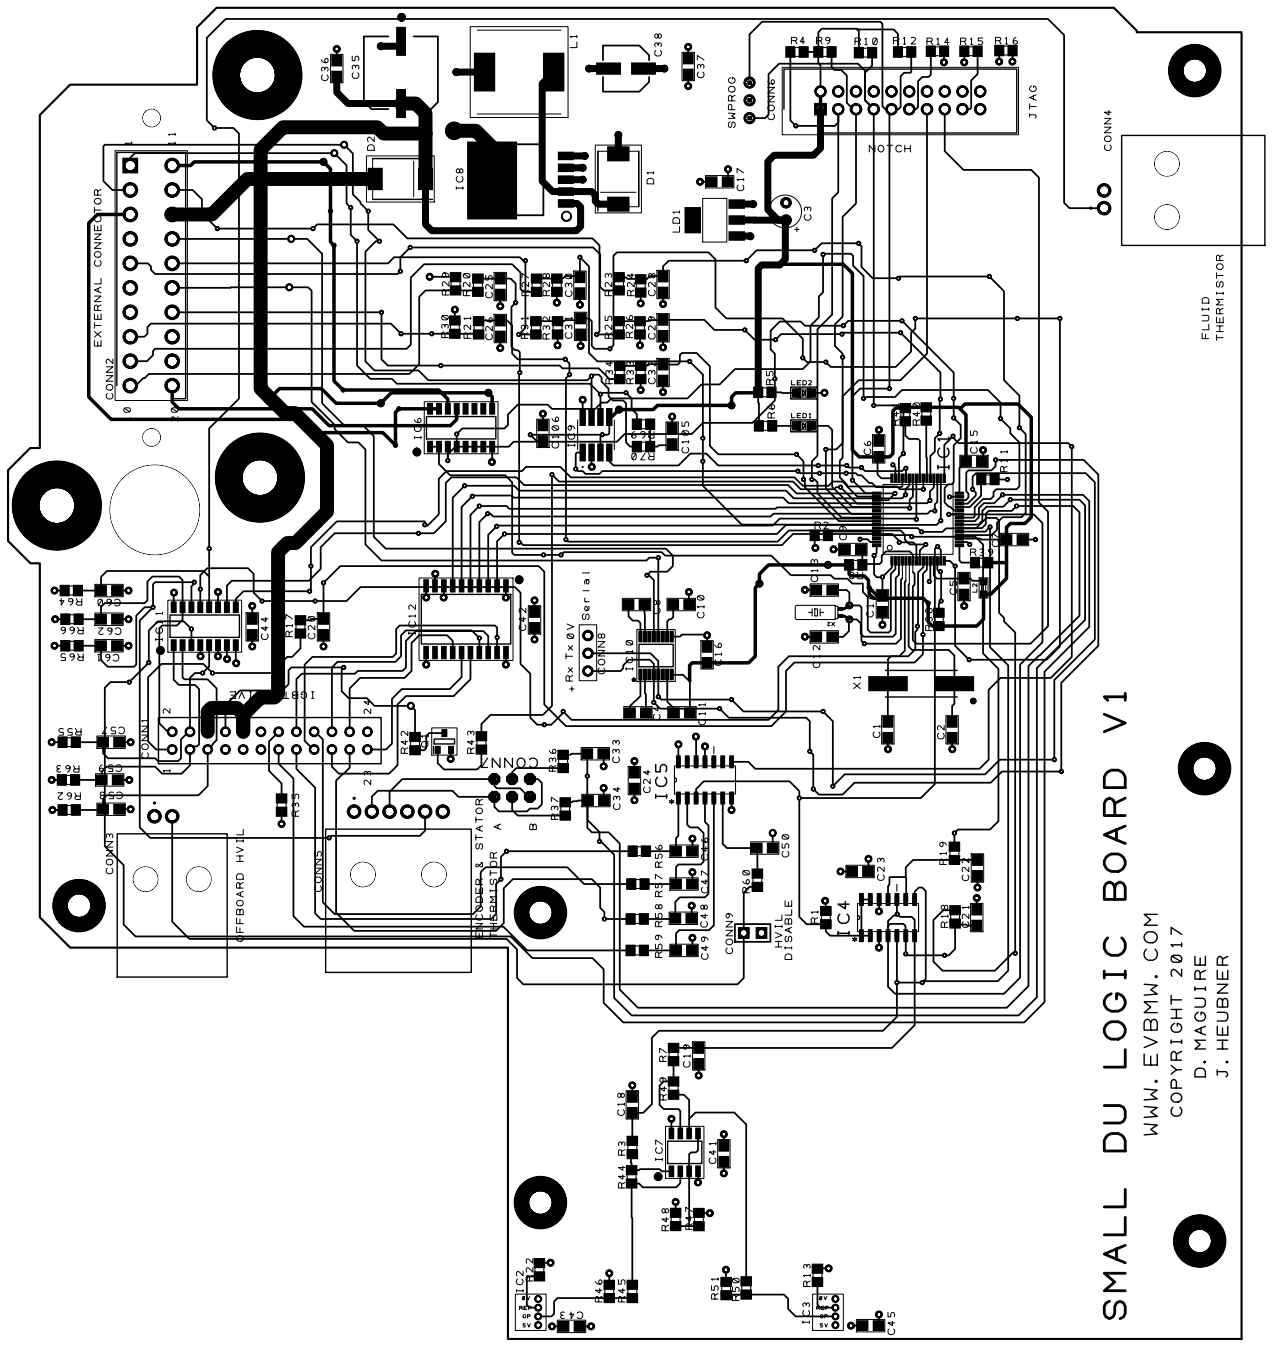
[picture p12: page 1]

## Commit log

2017-09-22 Add files via upload
    Autocad dxf file of board outline , hole positions and connectors for the Tesla front drive unit PCB.
    [Tesla_FDU_V1.dxf]
2021-10-07 Update Tesla_FDU_V6_BOM_JLC.xls
    Updated "Package" header to "Footprint" for compatibility with JLCPCB's recent SMT quoting changes
    [Tesla_FDU_V6_BOM_JLC.xls]
2025-11-16 Add Kicad project
